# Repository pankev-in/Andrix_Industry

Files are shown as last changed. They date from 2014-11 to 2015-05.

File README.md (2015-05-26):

# Andrix_Industry
AndriX in Industry Use - Practical Robotics Institute Austria (PRIA)

# About this Repository
Here you can find all files, Software and complete documentations used in this Project. Here is a link to a Youtube 
Video, where you can see it in action:
<a href="https://www.youtube.com/watch?v=nksSCDoHSoU">Hedgehog controller drives industrial motor (SCORE! project)</a>

# Who is PRIA?
The Practical Robotics Institute Austria (PRIA) is a non-profit organisation with the aim to promote scien-
tific and technical excellence in schools using robotics as well as the participation and operation of exemplary
research projects in fields related to robotics and automation and teaching methods by means of robotics.
The Practical Robotics Institute Austria is constituted as an independent non-profit organisation with a
scientific advisory board.

# Concept of this Project
Nowadays computers with ARM architecture are becomming more common. Various smartphones, as well
as sigle-board computers like Raspberry Pi are becomming cheaper and much more affordable. To be able
to use ARM Devices as robot controllers, some additional hardware that enables connecting and controlling
robot components such as sensors, motors and servos are required. The hardware (aka. Low-Level Control,
LLC) and the ARM devices(aka. High-Level Control, HLC) should be able to be connected together using
both wired and wireless communications.

Andrix Industry is the concept of implementing this kind of structure in an industrial environment and
its controller has to be relatively low-cost, stable and expandable for different uses.
In this project, we use a standard industrial conveyor belt to test our idea. We will connect our Andrix
controller (including an Raspberry Pi as the High level control) to an external Motor Controller (aka. Ex-
ternal Hardware Controller level) to be able to drive the conveyor belt using a Stepper Motor.

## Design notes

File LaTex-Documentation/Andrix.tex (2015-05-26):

\documentclass[11pt,a4paper]{article}

\usepackage{latexsym}
\usepackage[left=1.5cm,right=1.5cm,bottom=2.5cm,top=2.5cm]{geometry}
\usepackage{tikz} 
\usepackage{mathtools} %Math function
\usepackage{listings} %Source code
\usepackage{pdfpages} %PDF import

\pdfinfo{
	/Title (Andrix-Industry.pdf)
	/Creator (Kevin Pan)
	/Producer (PRIA Austria)
	/Author (Kevin Pan)
	/Subject (Andrix Industry - Sample Usage)
	/Keywords (Andrix, Industry, Sample)
}

\usepackage{graphicx}
\lstset{ 
numbers=left
}

\begin{document}

%----------------------------------------------------------------------------------------
%	TITLE PAGE
%----------------------------------------------------------------------------------------

\begin{titlepage}

\newcommand*{\titlePAGE}{\begingroup % Create the command for including the title page in the document
\hbox{ % Horizontal box
\hspace*{0.1\textwidth} % Whitespace to the left of the title page
\rule{1pt}{\textheight} % Vertical line
\hspace*{0.05\textwidth} % Whitespace between the vertical line and title page text
\parbox[b]{0.75\textwidth}{ % Paragraph box which restricts text to less than the width of the page

{\noindent\Huge\bfseries \textit{Andrix Industry} \\ Sample Usage}\\[2\baselineskip] % Title
{\large \textit{Practical Robotic Institude Austria}}\\
{\large \textit{TGM - The Institute of Technology Austria}}\\[1\baselineskip]
{\large \textbf{2015 May}}\\[4\baselineskip]
{\Large \textsc{Kevin Pan}}\\[1\baselineskip]% Author name
{\Large \textsc{Alexander Wurm}} % Author name

\vspace{0.5\textheight} % Whitespace between the title block and the publisher
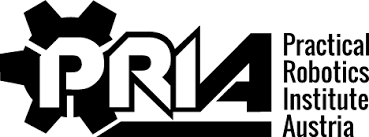
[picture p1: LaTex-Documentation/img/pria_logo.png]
{\noindent  }\\[\baselineskip] % Publisher and logo
}}
\endgroup}

\titlePAGE % This command includes the title page

\end{titlepage}

%----------------------------------------------------------------------------------------
%	CONTENT TABLE
%----------------------------------------------------------------------------------------

\newpage

\tableofcontents

%----------------------------------------------------------------------------------------
%	GENERAL
%----------------------------------------------------------------------------------------

\newpage
\part{Introduction}

	%###################################################
	%	ABOUT
	%###################################################

\section{About}
\subsection{PRIA}
The Practical Robotics Institute Austria (PRIA) is a non-profit organisation with the aim to promote scientific and technical excellence in schools using robotics as well as the participation and operation of exemplary research projects in fields related to robotics and automation and teaching methods by means of robotics. The Practical Robotics Institute Austria is constituted as an independent non-profit organisation with a scientific advisory board.\\

Robots are sophisticated, intelligent systems used in factories and everyday life. They allow students to connect theory with practice and exercise team work, project management, problem solving and communication skills in a stimulating setting. Robotics integrates all the skills needed for designing and constructing machines, computers, software, communications systems and networks. It conveys to students the flexibility needed for developing interdisciplinary projects and discovers exciting topics such as movement, navigation, coordination, physical interaction with objects, audio and video processing, cognition and recognition and many others. It also helps them in developing their abstract thinking and to acquire teamwork skills, independence, imagination and creativity. Experiments with robots include many hands-on experiments that make classes more dynamic and fun.\\

\subsection{Our Mission}

\begin{itemize}
  \item To use robotics technology as an instrument to prepare students to work with various mechanical, electrical and software systems.
  \item To develop environments and tools for teaching robotics that
    \begin{itemize}
    \item will enable simpler programing and control of robots,
    \item are easily interfaced with a broad range of sensors and effectors,
    \item can be used to investigate complex problems and tasks,
    \item are affordable and open for public use.
  \end{itemize}
  \item To introduce appropriate educational methodologies for the successful integration of robotics innovation in school classes.
  \item To organise robotics competitions and measure their educational impact.
  \item Create innovative control architectures for robotics and industrial automation.
  \item Develop knowledge-based systems and agent technology for the automation of flexible industrial processes.
  \item Introduce Augmented Reality and make visualization of industrial processes more efficient and easier to understand.
\end{itemize}

	%###################################################
	%	Concept
	%###################################################
\newpage
\section{Concept}
\subsection{Idea}
Nowadays computers with ARM architecture are becomming more common. Various smartphones, as well as sigle-board computers like Raspberry Pi are becomming cheaper and much more affordable. To be able to use ARM Devices as robot controllers, some additional hardware that enables connecting and controlling robot components such as sensors, motors and servos are required. The hardware (aka. Low-Level Control, LLC) and the ARM devices(aka. High-Level Control, HLC) should be able to be connected together using both wired and wireless communications.\\

\begin{figure}[htp]
	\centering
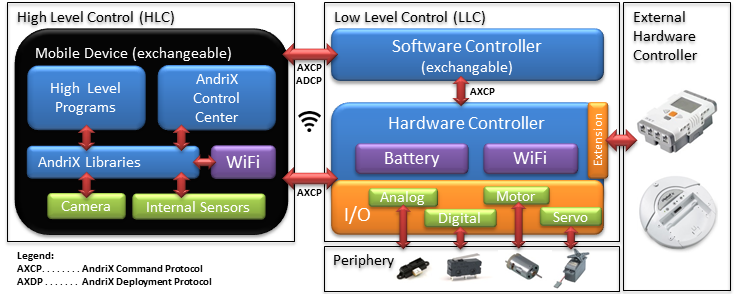
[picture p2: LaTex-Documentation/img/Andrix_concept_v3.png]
	
	\caption{Andrix Concept}
	\label{fig:Andrix Concept v3}
\end{figure}

Andrix Industry is the concept of implementing this kind of structure in an industrial environment and its controller has to be relatively low-cost, stable and expandable for different uses.\\

In this project, we use a standard industrial conveyor belt to test our idea. We will connect  our Andrix controller (including an Raspberry Pi as the High level control) to an external Motor Controller (aka. External Hardware Controller level) to be able to drive the conveyor belt using a Stepper Motor.\\

\begin{figure}[htp]
	\centering
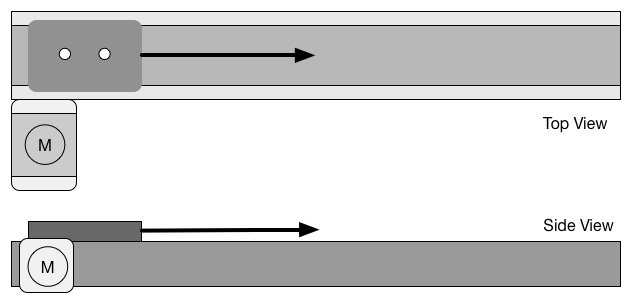
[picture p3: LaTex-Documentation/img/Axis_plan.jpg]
	
	\caption{conveyor belt with NEMA stepper motor}
	\label{fig:Axis Plan}
\end{figure}

THe NEMA Stepper motor series is one of the most popular motors in both amateur and professional fields. They are amazingly  accurate and powerful, but at the same time very easy to control.

	%###################################################
	%	Process
	%###################################################

\newpage
\section{Process}
\subsection{Project steps}
To be able to achive this goal, we planned the project precisely. The following provides a brief overview of our processes:

\begin{enumerate}
\item Choosing matching hardware 
\item Designing necessary mechanical parts
\item Producing mechanical parts by using CNC or 3D-printer 
\item Calculating needed supply power 
\item Designing external motor controller 
\item Prototyping electronic design
\item Communication protocol 
\item Software programming 
\item Debug, test and other final process 
\end{enumerate}

There are some different conditions which have to be satisfied to achieve our concept. At first, we need to find an industrial conveyor belt, which has to be samll enough to let us drive it easily with a stepper-motor without having too many problems. There are mainly two kinds of conveyor belt on the market today - limited and unlimited countineus conveying systems.\\

\subsection{Selecting a suitable conveyor belt}
Unlimited countineus conveying systems are the most common version and have been applied in various areas like raw meterial supply or warehouse transportation systems. They don't need any sesors to detects current position and can be controlled easily by changing the speed of the rotations. Limited conveyor belts work in principle familiar to continues system, but the position of the belt is controlled precisely use servo motor and has integrated sensors working with Hall effect(magnet) or IR encoders(light), but both of them need an extra circuit to drive them and need an externel programme to decode the position.\\

\subsection{Selecting actuator}
This is also one of the reasons why we use a stepper motor. NEMA stepper motors are in comparision to other motors much more flexible. It can be controlled easily with two H-Bridge Motor controller or FET-Transistors. We can dettect the position just by counting the steps in the register from the microcontroller. Of course it also has a disadvantage - speed. The accurency and the speed of the motor are proportional to each other and in our case, this can lead to inaccuracies by changing the step resolution, which is not a mechanical problem that can be easily avoided.\\

\subsection{Communication}
An agreement for the communication protocol between the Andrix and the external motor controller has to be made too. We are using 9600 bit/s as our communication speed. It is a standard bandwidth and can be controlled by other computers. The electronic controller has to be choosed carefully. We have to calculate and test the maximum supply current the motor need to run stably and compare it with the datasheet from the manufactuer.\\

\begin{figure}[htp]
	\centering
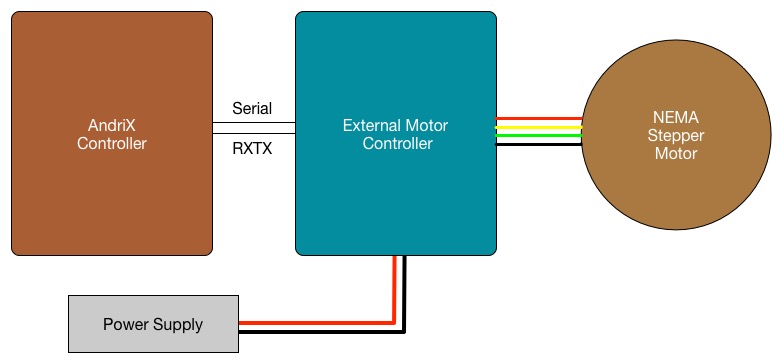
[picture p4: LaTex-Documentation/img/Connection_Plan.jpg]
	
	\caption{Control Flow}
	\label{fig:Axis Plan}
\end{figure}

%----------------------------------------------------------------------------------------
%	DESIGN
%----------------------------------------------------------------------------------------

\newpage
\part{Design}

	%###################################################
	%	Mechanic
	%###################################################
\section{Mechanics}

\subsection{conveyor belt and Axis}

For the conveyor belt, we chose the Bosch RExroth CKR linear motion series. The CKR Compact Modules are precision, ready-to-install linear systems offering high performance within a compact envelope and selectable length, combined with an economical price-to-performance ratio.\\

\textbf{Construction:}
\begin{itemize}
	\item Extremely compact precision aluminum profile with two integrated ball rail guides for optimal movement of heavy loads at high speeds
	\item Ready-to-install Compact Modules in selectable lengths up to Lmax
	\item Short or long aluminum carriage lengths available, depending on application load
	\item Driven by a pre-tensioned, steel-cord reinforced polyurethane toothed belt\\
\end{itemize}

\textbf{Optional Components:}
\begin{itemize}
	\item Maintenance free digital servo drives with integrated brake and pre-installed feedback
	\item Gear Reduced type LP
	\item REED or HALL sensor switches available
	\item Socket with terminals for connection switches
	\item Aluminum profile cable duct for easy mounting of switches\\
\end{itemize}

\textbf{Capabilities:}
\begin{itemize}
	\item Speed - up to 5 m/s
	\item Load Capacity C - up to 56,530 N
	\item Length - up to 5,500mm
	\item Height - 40mm to 65mm
	\item Static Loading - up to 200kg
\end{itemize}

\includepdf[pages=-]{cad/CKR_110_NN_1_69.PDF}
\includepdf[pages=-,landscape]{cad/CKR_110.PDF}

\newpage
\subsection{Actuator and motor}
The motor we are using is QSH5718-76-28-189 from TRINAMIC. It is a two phase hybird stepper motors optimized for microstepping and gives a good fit to high accurate control.\\

\textbf{Specification:}
\begin{itemize}
	\item NEMA 23 mounting Configuration
	\item Number of Leads:	4
	\item Step angle:	1.8
	\item Step Angle Accuracy:	0.05
	\item Holding Torque:	1.89 Nm
	\item Max app. Voltage: 75V
	\item Max Current:	2.8A /Phase	
	\item Max Temp. Rise:	+80
	\item Weight:	1kG
	\item Dimensions(mm):	56.5 x 56.5 x 76
\end{itemize}
\begin{figure}[h!]
	\centering
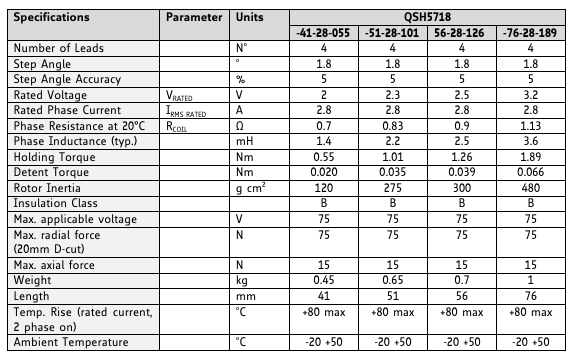
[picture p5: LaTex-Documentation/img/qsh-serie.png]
	
	\caption{Specifications of QSH5718 Series}
	\label{fig:Specifications of QSH5718 Series}
\end{figure}

\includepdf[pages=6-7]{cad/QSH5718_manual.pdf}
\includepdf[pages=10]{cad/QSH5718_manual.pdf}
\includepdf[pages=-,landscape]{cad/Stepper-motor-NEMA-23HS7430.PDF}
\includepdf[pages=-,landscape]{cad/CAD_Assembly.PDF}

	%###################################################
	%	Electronic
	%###################################################
\newpage
\section{Electronics}
\subsection{External motor control unit}

The external motor control unit consists of 2 different boards. One board is responsible for communication and translates the commands from the Andriox controler to the actual PWM signal and direction output. Another part of this unit is the motor controller. As the requirement, our stepper motor is bipolar and contents 4 wires. Two in a pair and each pair is only responsible for one coil.\\

\begin{figure}[h!]
	\centering
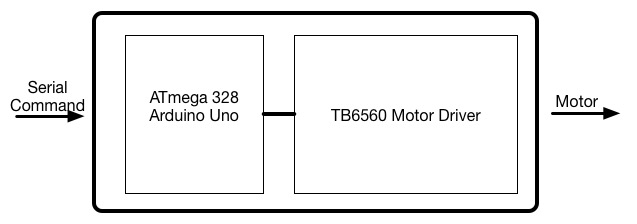
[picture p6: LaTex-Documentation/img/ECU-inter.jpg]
	
	\caption{ECU Overview}
	\label{fig:ECU Overview}
\end{figure}

For communication we decided to use a prototype board - Arduino uno. On the board is a ATmega 328 and has built-in serial communication pins. The standard Arduino IDE has pre implemented libraries for both serial and PWM signals.\\

The same as the describtion from the NEMA 23 Motor data sheet, we also found a stepper motor driver with required output current. The core of this board is a Toshiba dual H-bridge chip TB6560.\\

%Motor Requierment and Data sheet from tb6560 motor driver
\begin{table}[h!]
\centering
\begin{tabular}{ ||l | l ||}
	\hline
	Model & QSH 5718-76-28-189\\
	Max. Voltage & 75 V\\
	Rated phase current & 2.8 A\\
	Number of leads & 4\\
	\hline
\end{tabular}
\caption{NEMA 23 requierment} 
\end{table}
\begin{table}[h!]
\centering
\begin{tabular}{|| l | l ||}
	\hline
	Operating Voltage & 12 - 36 V\\
	Max. Output current & 1.5 - 3 A/phase\\
	Drive type & Double-pole const. PWM\\
	Compatible Stepper motors & 4/6/8 leads\\
	\hline
\end{tabular}
\caption{TB6560 Data sheet} 
\end{table}

\begin{figure}[h!]
	\centering
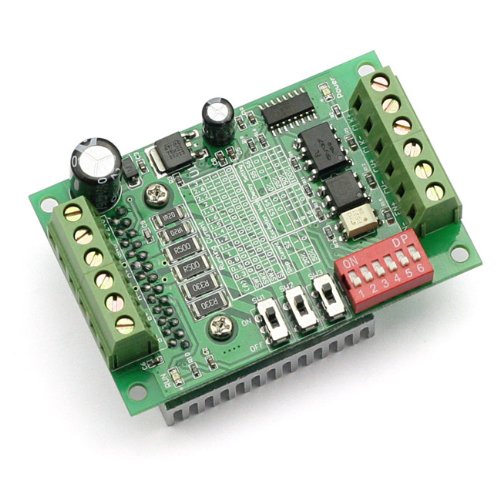
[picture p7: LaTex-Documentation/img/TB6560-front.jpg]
	
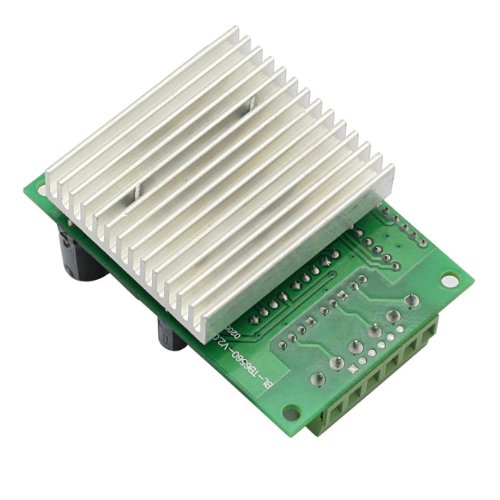
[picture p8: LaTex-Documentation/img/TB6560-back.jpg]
	
	\caption{TB6560 Stepper Motor Driver Module}
	\label{fig:TB6560 Stepper Motor Driver Module}
\end{figure}

\subsection{Power supply}

As we are suppplying our motor with 12V, the calculation of the power consumption will be like this:\\

\begin{equation}
   \text{Total power }P_t  = \text{External Control Unit } P_e + \text{Motor }P_m
\end{equation}
\begin{equation}
   P_m = I_o \times U_i = 3A \times 12V = 36 W 
\end{equation}
\begin{equation}
   P_m \gg P_e \text{ ,so }  P_m \approx P_t
\end{equation}
\\

Our power supply must able to supply at least 40 Watts of power to drive our converying belt and control units.

\newpage
\subsection{Overall circuit}

\begin{figure}[h!]
	\centering
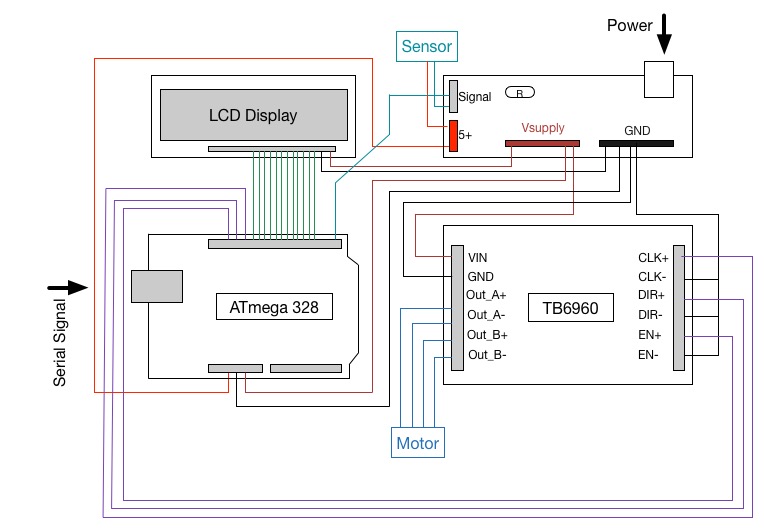
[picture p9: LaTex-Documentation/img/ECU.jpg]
	
	\caption{External Control Unit: cabling}
	\label{fig:External Control Unit: cabling}
\end{figure}

	%###################################################
	%	Software
	%###################################################
\newpage
\section{Software - Ecu}
\subsection{Logical equivalence }
The system logic of the external motor controller has 3 main states: initial, processing and waiting process:\\
\begin{figure}[h!]
	\centering
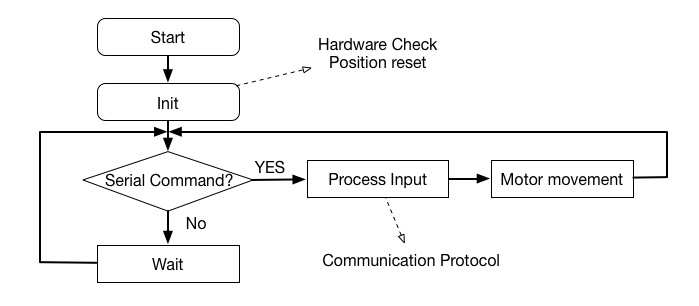
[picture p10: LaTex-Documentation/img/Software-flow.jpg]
	
	\caption{Software Logic}
	\label{fig:Software logic}
\end{figure}\\

In the boot up phase, the system will first check if all the hardware is connected and reset the position automatically. It sends continuous signals to the motor to move the conveying base back to the origin and if the base has a physical contact with it, the digital sensor will set its output to HIGH.\\

After the reboot, the system is ready and waits for the serial command from the andrix or PCs. The serial bandwidth has already been set in the initial process and the default is 9600bit/s. Any serial signal during the waiting phase will be stored in a String buffer to futher process. The conmunication will be base on the protocol from \textbf{section 6.3}.

\subsection{Function description}
To find more detail of a specific function, please go to \textbf{section 6.4}.\\
\begin{table}[h!]
\centering
\begin{tabular}{ |l | l | c |c |}
	\hline
	Name & Use & Input & Return\\
	\hline
	setup() & Init Setup & --- & ---\\
	loop() & Main loop & --- & depend\\
	serialEvent() & Reading Serial Input and buffer them & --- & ---\\
	reset() & Reset position to origin & --- & ---\\
	goToPosition() & Go to position & Integer & ---\\
	lcdShow() & Display message on LCD Display & String 1,2 & ---\\
	lcdBackLightOnOff()   & Turn LCD Light On or Off & boolean & ---\\
	\hline
	
\end{tabular}
\end{table}

\newpage
\subsection{Communication protocol}
\begin{table}[h!]
\centering
\begin{tabular}{ ||l | l | l ||}
	\hline
	Command & Description & Sample\\
	...@ & @ - end; ... - Commands & Bandwith = 9600 bit/sec \\ \hline\hline
	ENA@ &Enable the motor & Send: \textbf{ENA@} -- Motor enabled\\
	DIS@ &Disable the motor& Send: \textbf{DIS@} -- Motor disabled\\
	RES@ &Reset, back to origin& Send: \textbf{RES@} -- Axis back to 0 position\\
	GTP...@ & Go to xxx/10 mm position	[Max. 4950]& Send: \textbf{GTP1234@} -- Axis go to 123.4mm\\
	SST...@ & Set delay of motor(default 0)	[2 byte]& Send: \textbf{SST1@} -- Set 1 ms delay for each step\\
	CTP@ & send back to the current position [2 byte]& Send: \textbf{CTP@};Return: \textbf{123@}  -- Current Position\\
	CTS@ & send back the current speed(delay) [2 byte]& Send: \textbf{CTS@};Return: \textbf{1@}  -- Current Delay\\	
	LED...@ & Turn LED Display light ON or Off & Send: \textbf{LED1@}--Light turn On\\
		\hline
\end{tabular}
\caption{Protocol: Stepper Motor Control} 
\end{table}

If you want to modify the setting of the communication bandwidth, you will have to programme the external control unit with the source code from \textbf{6.4} using Arduino IDE.\\

\textbf{Communication sample:}
\begin{lstlisting}
Normal Operation:
1.SEND:		ENA@		\\Enables the motor
2.SEND:		GTP1000@	\\Go to Position 10cm
3.SEND:		RES@		\\Reset position to 0, all default value

Move Slowly:
1.SEND:		ENA@		\\Enables the motor
2.SEND:		SST1@		\\Set Delay for 1ms
3.SEND:		GTP500@		\\Convayingbelt will move slowly to 5cm

Let conveyor belt to be able to move by hand:
1.SEND:		DIS@		\\Disable the motor
2.SEND:		RES@		\\WARNING:You must reset the position!

Turn On/Off LED Display backlight:
1.SEND:		LED1@		\\Turn On light
2.SEND:		LED0@		\\Turn Off light
3.SEND:		LED3@		\\Turn On light(Any num.>0 will be 'ON')

\end{lstlisting}

\newpage
\subsection{Source code}
\lstinputlisting[language=C]{code/Stepper_Low_Power.c}

%----------------------------------------------------------------------------------------
%	CONCLUTION
%----------------------------------------------------------------------------------------
\newpage
\part{Conclution} 
After assembling the mechanical design and putting all electronic components together, we devised a very simple system. We tested the axis accuracy and it is much more percise than we first expected.\\
\section{Resaults and Comparison}

In comparison with some of the industrial standard machines, our solution can be up to 10 times cheaper. Of course, the standard system can control/supply multiple linear or even other kinds of axises at the same time. But one of the biggest advantages of distributed system is flexibility.\\

Unter the same kind of hardware structure, we are able to connect multiple controllers with a central computer, and control them induvidually. It is also even posible to implement some kind of smart algorithm, which is designed spicificly for each individual enviroment.\\

In this example we only show one way of using an Andrix controller in Industrial area. It shows us the potential of distributed system and can be one of the most important keys for 'Industrial 4.0'. It will change the way we look at the normal rigid structure.\\

\end{document}
\grid
\grid

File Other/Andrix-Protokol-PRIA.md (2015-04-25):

## Andrix - Protokol: PRIA

### About PRIA(Wurm)[1]

### Team(Wurm)[1]

### Concepte(PAN)[2]
* Was ist Andrix?
* Vorteile?
* Unsere Idee mit Andrix Industrie?
* Concept plan

### Umsetzung(PAN)[1]
* Arbeitsschritte
* Unterschiede zwischen 2 motoren/Achsen
* Wir nehmen NEMA 23 als Beispiel

### Mechanic(PAN)[3,4]
* Achse:
	* Model nummer
	* länge/breite/gröse
	* beschränkungen zu beachten
	* Datenblatt (falls es gibt)
	* CAD Zeichnung 
* Motor:
	* Gröse, Stärke 
	* Drehmoment
	* Maximale Drehzahl
	* Datenblatt
	* CAD Zeichung
* Wellenadapter:
	* Warum brauchen wir es? Problem beschreibung
	* Meterial Auswall
	* Messungen
	* CAD Zeichnung
* Gesamt:
	* Messungen
	* CAD Zeichnung  
* Fotos von end produkten

### Electronik(Wurm)[3]
* Andrix:
* External Motor Steuerung:
	* Welche leistung hat der motor? 
	* Welche leistung muss diese Krontroller treiben können?
	* Steuerungsverlauf
		* Bild
		* Beschreibung
	* Power supply
	* Interne Schaltungs plan (friztzing oder co.)
* Fotos von end produkten

### Software(Wurm)[3,4]
* Control bzw. Logische Verlauf
* Funktion beschreibung
* Source Code mit genaue Commendar dazu

### Conclutions(PAN)[2]
* Testergebnisse: Gut? Schlecht?
* Vergleich mit Industrie Standard Steuerung:
	* Preis
	* Flexibilität
	* Erweiterungsmöglichkeit(Open Source?)
	* Größe
* Idee mit Industrie 3.0 zusammen verbinden

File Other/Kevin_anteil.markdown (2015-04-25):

## Concept

Nowadays computers under ARM architecture are getting common. Variate smartphones, sigle-board computers like Raspberry Pi are getting cheaper and much more affordable. To be able to use ARM Devices as robot controllers, some additional hardware that enables connecting and controlling robot components such as sensors, motors and servos are required. The hardware (aka. Low-Level Control, LLC) and the ARM devices(aka. High-Level Control, HLC) should be able to be connected together using both wired and wireless communications. The following figure illustrates the concept:



AndriX Industry is the concept of implementing this kind of structure in a industrial environment and its controller has to be low-cost(relatively), stable and expansional for different uses.

In this project, we are using a standard industrial conveying belt to test our idea. We will connect  our Andrix controller (including an Raspberry Pi as the High level control) to a external Motor Controller (aka. External Hardware Controller level) to be able to drive the conveying belt using a Stepper Motor.

NEMA Stepper motor series is one of the most popular Motors in both pre-industrial and professional fields. It is amazingly  accurate and powerful, but at the same time very easy to control.

## Processes

To be able to achive the goal, we planned the project precisely and here is a quick overall view of our working processes:

1. Choosing matching hardware
2. Designing other mechanical parts we need
3. Producing mechanic parts by using CNC or 3D-printer
4. Calculate needed supply power 
5. Design external motor controller
6. Prototyping electronic design
7. Communication protocol
8. Software programming
9. Debug, test and other finalisation process

There are some different conditions have to be satisfied to achieve our concept. At first, we need to find a industrial conveying belt, which has to be samll enough to let us drive it easily with one stepper-motor without having too many problems. There are mainly two kind of conveying belt on the market today - limited and unlimited countineus conveying Systems. 

Unlimited countineus conveying systems are the most common version and have been applicated in various areas like raw meterial supplyment or warehaus transportation systems. They don’t need any sesors to detect current position and can be controlled easily by changing the speed of the rotations. Limited conveying belts works in principle familiar to countineus system, but the position of the belt is controlled precisely using servo motor and has integrated sensors working with hall effect(magnet) or IR encoders(light), but both of them need extra circuit to drive them and need externel programm to decode the position.

This is also one of the reason why we use stepper motor. NEMA stepper motors are in compare to other motors much more flexible to control. It can be controlled pretty easily with two H-Bridge Motor controller or FET-Transistors. We can dettect the position just by counting the steps in the register from the microcontroller. Of course it also has disadvantage - speed. The accurency and the speed of the motor are proportional to each other and in our case, we can lose our accurency by changing the step resolution, which isn’t a mechanical problem that can be simply avoided.

An agreement for the communication protocol between the andrix and the external motor controller has to be made too. We are using 9600 bit/s as our communication speed. It is a standard bandwitdh and can be even controlled with other computers. The electronic controllers has to be choosed carefully. We have to calculate and test the maximum supply current the motor needed to run stabely and compare it with the datasheet from the manufacture.

## Mechanic
### Overview:IEF profiLine 140
### Conveying belt
### Motor
### Shaft Adapter

## Conclutions

aasdfas

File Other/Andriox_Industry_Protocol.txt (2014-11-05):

Androix Industry: Industrie Motor / Robotic Steuerung
  Autor: Kevin Pan
  Date: 09.2014 - 11.2014

###############################################################################
Introduction:

  "Androix" Controller is an easy-to-programm, educational robotic controller.It
  is developed by Practical Robotic Institute Austria (As known as PRIA). Located
  at TGM, a technical Institute in Vienna, Austria.

  Andriox is designed for everybody, who wanted to build their own DIY-Robots,
  but didn't know where to start with. Andriox allows users to program their
  robot without any knowledges. You can simply program the robot using any kind
  of smartphones. There are graphical API for Androix running on Android, IOS,
  Windows, OSX or even Linux.

  The basic Idea of the "Androix-Industry" project is to use this simple controller
  to controll Industrial-level Motors/Axis. Which allows the Instructors to have
  a low-cost, stable, expansional to achieve the Idea of "Industrial 3.0".

###############################################################################
Setup:

  In this project, we are using NEMA Stepper motors to test our idea. NEMA
  Stepper-motor series is one of the most popular Motors for both pre-industrial
  uses and professional levels. It is very accurate and powerful, but at the same
  time easy to control.

  We chose two kind of NEMA Motors here:
    - 1x NEMA 23 (QSH 5718-76-28-189)
    - 1X NEMA 34 (QSH 8618-96-55-700)

  Both motor above are standard motors, which has been used in Robotic Industry
  or even as light-weight machine axis. NEMA 23/34 operates normally between
  12-24 V and requiers a extern power supply. But to be able to control the motor,
  we would need a extension module between the Androix Controller and the actual
  physical Motor.

  Here is the Controll flow(foto):

                  ########################################
                  #                                      #
                  #                                      #
                  #                                      #
                  #                                      #
                  #                                      #
                  ########################################

###############################################################################
Extension-Module:

  NEMA 23 specification:
      ∙ Type: Bipolar Stepper motor (4 wires)
      ∙ Ideal Voltage: 12-24 V (Vmax: 75V)
      ∙ Stall current: 2.8A (Max)

  NEMA 34 specification:
      ∙ Type: Bipolar Stepper motor (4 wires)
      ∙ Ideal Voltage: 24-36 V (Vmax: 75V)
      ∙ Stall current: 5.5A (Max)

  Control Module requirements:
      ∙ Stable
      ∙ Accuration
      ∙ Read serial commands from Androix
      ∙ Minimal Connections between the Controller and Androix
      ∙ Supply Motor with ideal voltage/current
      ∙ Scalability

###############################################################################
Andoix-Programming:

###############################################################################
Stability:

###############################################################################
Cost:

###############################################################################
Expansibility:

###############################################################################
Summary:

###############################################################################
Contact:

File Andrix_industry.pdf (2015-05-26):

# Andrix Industry Sample Usage

Practical Robotic Institude Austria
TGM - The Institute of Technology Austria

2015 May

Kevin Pan

Alexander Wurm

## Contents

I | Introduction | 2
1 About | 2
2 Concept | 3
3 Process | 4
II | Design | 6
4 Mechanics | 6
5 Electronics | 16
6 Software - Ecu | 19
III | Conclution | 26
7 Resaults and Comparison | 26

## Part I

# Introduction

## 1 About

### 1.1 PRIA

The Practical Robotics Institute Austria (PRIA) is a non-profit organisation with the aim to promote scientific and technical excellence in schools using robotics as well as the participation and operation of exemplary research projects in fields related to robotics and automation and teaching methods by means of robotics. The Practical Robotics Institute Austria is constituted as an independent non-profit organisation with a scientific advisory board.

Robots are sophisticated, intelligent systems used in factories and everyday life. They allow students to connect theory with practice and exercise team work, project management, problem solving and communication skills in a stimulating setting. Robotics integrates all the skills needed for designing and constructing machines, computers, software, communications systems and networks. It conveys to students the flexibility needed for developing interdisciplinary projects and discovers exciting topics such as movement, navigation, coordination, physical interaction with objects, audio and video processing, cognition and recognition and many others. It also helps them in developing their abstract thinking and to acquire teamwork skills, in-dependence, imagination and creativity. Experiments with robots include many hands-on experiments that make classes more dynamic and fun.

### 1.2 Our Mission

- To use robotics technology as an instrument to prepare students to work with various mechanical, electrical and software systems.
- To develop environments and tools for teaching robotics that

– will enable simpler programing and control of robots,

– are easily interfaced with a broad range of sensors and effectors,

– can be used to investigate complex problems and tasks,

– are affordable and open for public use.

- To introduce appropriate educational methodologies for the successful integration of robotics innova-tion in school classes.
- To organise robotics competitions and measure their educational impact.
- Create innovative control architectures for robotics and industrial automation.
- Develop knowledge-based systems and agent technology for the automation of flexible industrial processes.
- Introduce Augmented Reality and make visualization of industrial processes more efficient and easier to understand.

## 2 Concept

### 2.1 Idea

Nowadays computers with ARM architecture are becomming more common. Various smartphones, as well as sigle-board computers like Raspberry Pi are becomming cheaper and much more affordable. To be able to use ARM Devices as robot controllers, some additional hardware that enables connecting and controlling robot components such as sensors, motors and servos are required. The hardware (aka. Low-Level Control, LLC) and the ARM devices(aka. High-Level Control, HLC) should be able to be connected together using both wired and wireless communications.

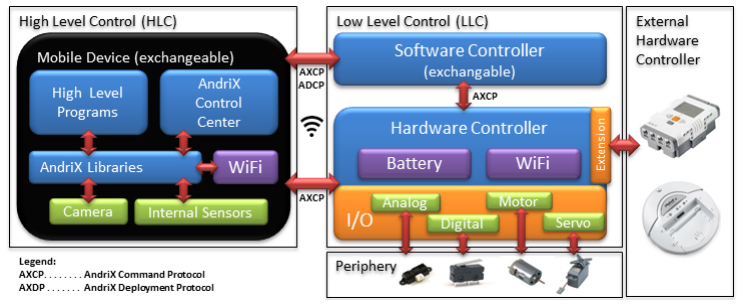
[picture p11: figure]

Figure 1: Andrix Concept

Andrix Industry is the concept of implementing this kind of structure in an industrial environment and its controller has to be relatively low-cost, stable and expandable for different uses.

In this project, we use a standard industrial conveyor belt to test our idea. We will connect our Andrix controller (including an Raspberry Pi as the High level control) to an external Motor Controller (aka. External Hardware Controller level) to be able to drive the conveyor belt using a Stepper Motor.


Figure 2: conveyor belt with NEMA stepper motor

THe NEMA Stepper motor series is one of the most popular motors in both amateur and professional fields. They are amazingly accurate and powerful, but at the same time very easy to control.

## 3 Process

### 3.1 Project steps

To be able to achive this goal, we planned the project precisely. The following provides a brief overview of our processes:

1. Choosing matching hardware
2. Designing necessary mechanical parts
3. Producing mechanical parts by using CNC or 3D-printer
4. Calculating needed supply power
5. Designing external motor controller
6. Prototyping electronic design
7. Communication protocol
8. Software programming
9. Debug, test and other final process

There are some different conditions which have to be satisfied to achieve our concept. At first, we need to find an industrial conveyor belt, which has to be samll enough to let us drive it easily with a stepper-motor without having too many problems. There are mainly two kinds of conveyor belt on the market today -limited and unlimited countineus conveying systems.

### 3.2 Selecting a suitable conveyor belt

Unlimited countineus conveying systems are the most common version and have been applied in various areas like raw meterial supply or warehouse transportation systems. They don’t need any sesors to detects current position and can be controlled easily by changing the speed of the rotations. Limited conveyor belts work in principle familiar to continues system, but the position of the belt is controlled precisely use servo motor and has integrated sensors working with Hall effect(magnet) or IR encoders(light), but both of them need an extra circuit to drive them and need an externel programme to decode the position.

### 3.3 Selecting actuator

This is also one of the reasons why we use a stepper motor. NEMA stepper motors are in comparision to other motors much more flexible. It can be controlled easily with two H-Bridge Motor controller or FET-Transistors. We can dettect the position just by counting the steps in the register from the microcontroller. Of course it also has a disadvantage - speed. The accurency and the speed of the motor are proportional to each other and in our case, this can lead to inaccuracies by changing the step resolution, which is not a mechanical problem that can be easily avoided.

### 3.4 Communication

An agreement for the communication protocol between the Andrix and the external motor controller has to be made too. We are using 9600 bit/s as our communication speed. It is a standard bandwidth and can be controlled by other computers. The electronic controller has to be choosed carefully. We have to calculate and test the maximum supply current the motor need to run stably and compare it with the datasheet from the manufactuer.


Figure 3: Control Flow

## Part II

# Design

## 4 Mechanics

### 4.1 conveyor belt and Axis

For the conveyor belt, we chose the Bosch RExroth CKR linear motion series. The CKR Compact Modules are precision, ready-to-install linear systems offering high performance within a compact envelope and selectable length, combined with an economical price-to-performance ratio.

Construction:

- Extremely compact precision aluminum profile with two integrated ball rail guides for optimal movement of heavy loads at high speeds
- Ready-to-install Compact Modules in selectable lengths up to Lmax
- Short or long aluminum carriage lengths available, depending on application load
- Driven by a pre-tensioned, steel-cord reinforced polyurethane toothed belt

Optional Components:

- Maintenance free digital servo drives with integrated brake and pre-installed feedback
- Gear Reduced type LP
- REED or HALL sensor switches available
- Socket with terminals for connection switches
- Aluminum profile cable duct for easy mounting of switches

Capabilities:

- Speed - up to 5 m/s
- Load Capacity C - up to 56,530 N
- Length - up to 5,500mm
- Height - 40mm to 65mm
- Static Loading - up to 200kg

# CKR 15-110 dimensions

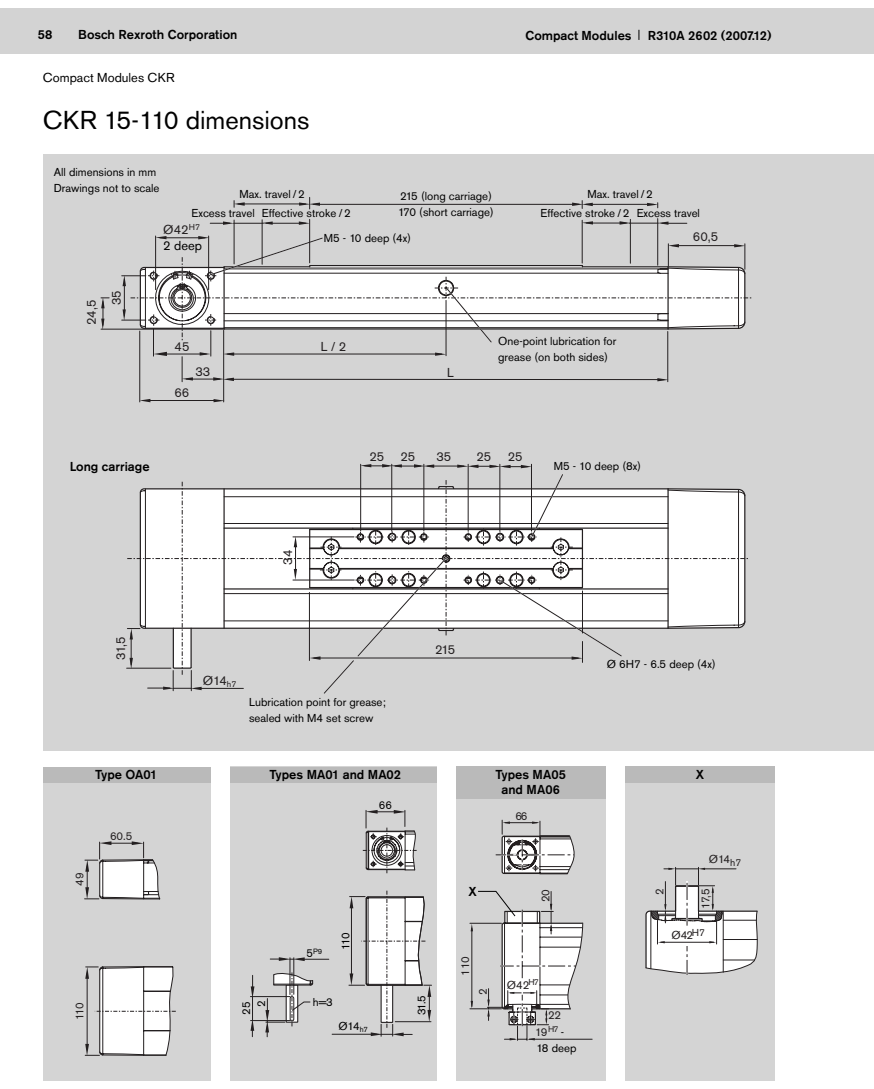
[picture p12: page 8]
Bosch Rexroth Corporation; Compact Modules; Long carriage; M5 - 10 deep (8x); 215 (long carriage) 170 (short carriage); M5 - 10 deep (4x); Max. travel/2; Ø 6H7 - 6.5 deep (4x); - 18 deep; Type OA01; Types MA01 and MA02; Types MA05; and MA06

Compact Modules CKR

All dimensions in mm
Drawings not to scale

Excess travel Effective stroke /2
2 deep

Effective stroke /2 Excess travel

One-point lubrication for
grease (on both sides)

Lubrication point for grease;
sealed with M4 set screw

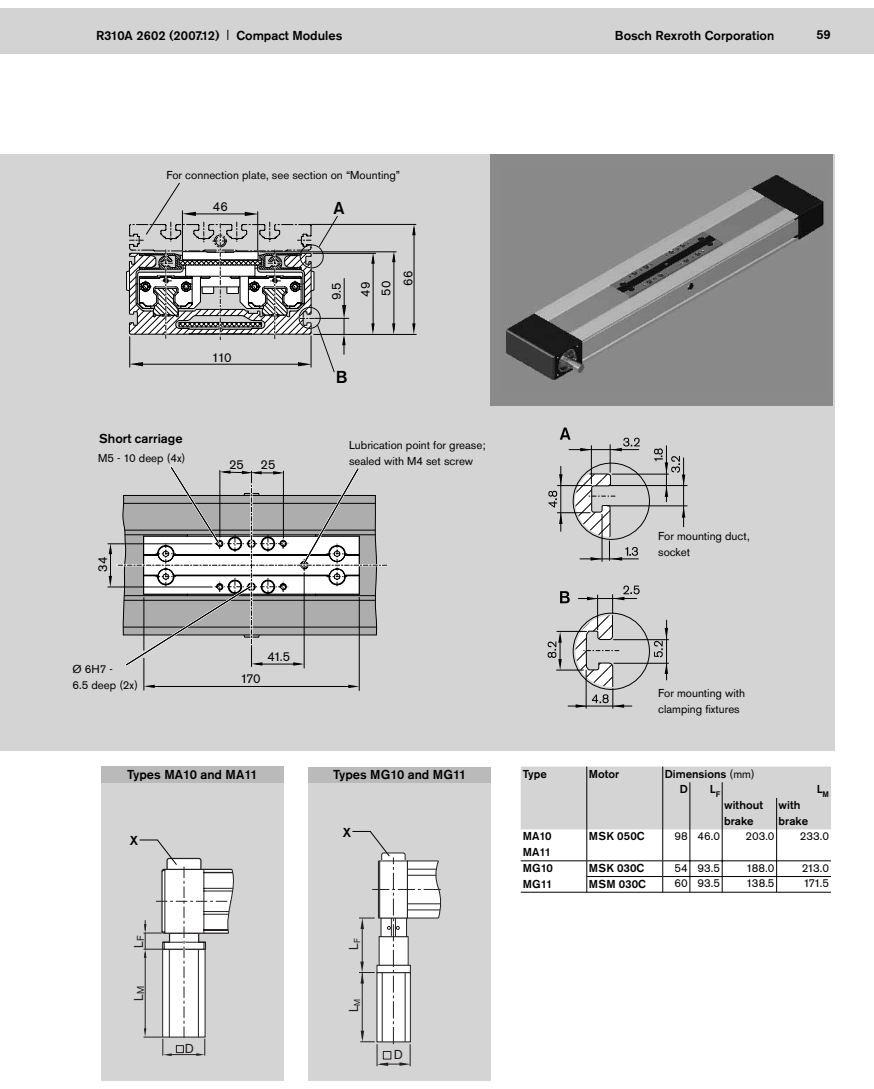
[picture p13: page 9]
Compact Modules; Bosch Rexroth Corporation; Short carriage; M5 - 10 deep (4x); Ø 6H7 - 6.5 deep (2x); MSK 050C; MSK 030C; MSM 030C; Types MA10 and MA11; Types MG10 and MG11

For connection plate, see section on “Mounting”

Lubrication point for grease;
sealed with M4 set screw

For mounting duct,
socket

For mounting with
clamping fi xtures

Type | Motor | Dimensions (mm)

without brake | with brake

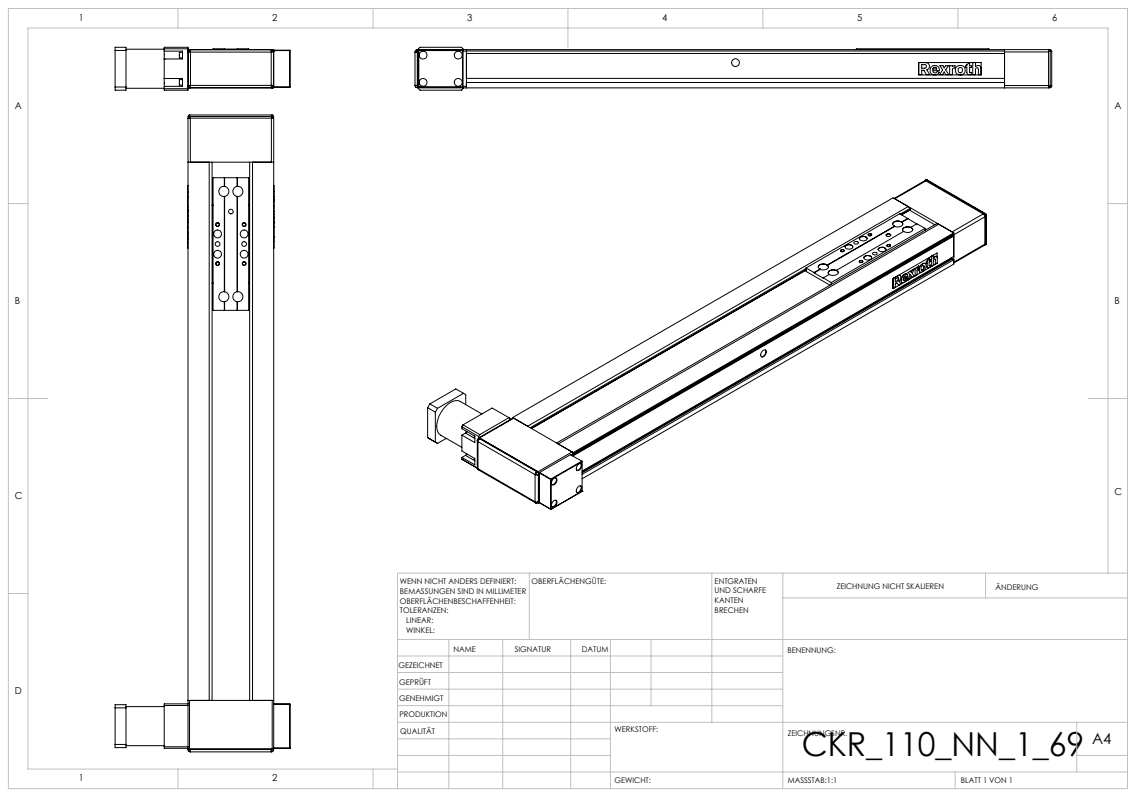
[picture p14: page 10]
OBERFLÄCHENGÜTE:; ENTGRATEN; UND SCHARFE KANTEN BRECHEN; ZEICHNUNG NICHT SKALIEREN; ÄNDERUNG; MASSSTAB:1:1; BLATT 1 VON 1; GEWICHT:

WENN NICHT ANDERS DEFINIERT:
BEMASSUNGEN SIND IN MILLIMETER
OBERFLÄCHENBESCHAFFENHEIT:
TOLERANZEN:
LINEAR:
WINKEL:

NAME | SIGNATUR | DATUM | | | | BENENNUNG:

GEZEICHNET
GEPRÜFT
GENEHMIGT
PRODUKTION
QUALITÄT | | | | WERKSTOFF: | CKR_110_NN_1_69 ZEICHNUNGSNR. | A4

### 4.2 Actuator and motor

The motor we are using is QSH5718-76-28-189 from TRINAMIC. It is a two phase hybird stepper motors optimized for microstepping and gives a good fit to high accurate control.

Specification:

- NEMA 23 mounting Configuration
- Number of Leads: 4
- Step angle: 1.8
- Step Angle Accuracy: 0.05
- Holding Torque: 1.89 Nm
- Max app. Voltage: 75V
- Max Current: 2.8A /Phase
- Max Temp. Rise: +80
- Weight: 1kG
- Dimensions(mm): 56.5 x 56.5 x 76

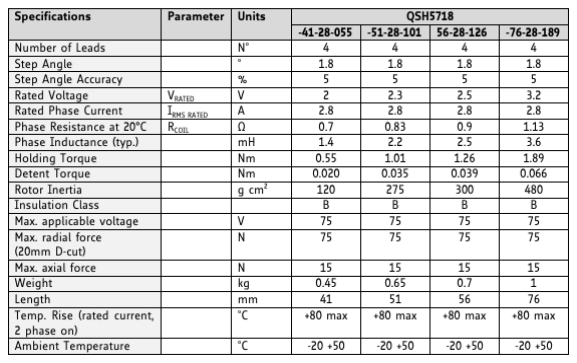
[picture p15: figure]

Figure 4: Specifications of QSH5718 Series

# 4 Mechanical dimensions

## 4.1 Dimensions

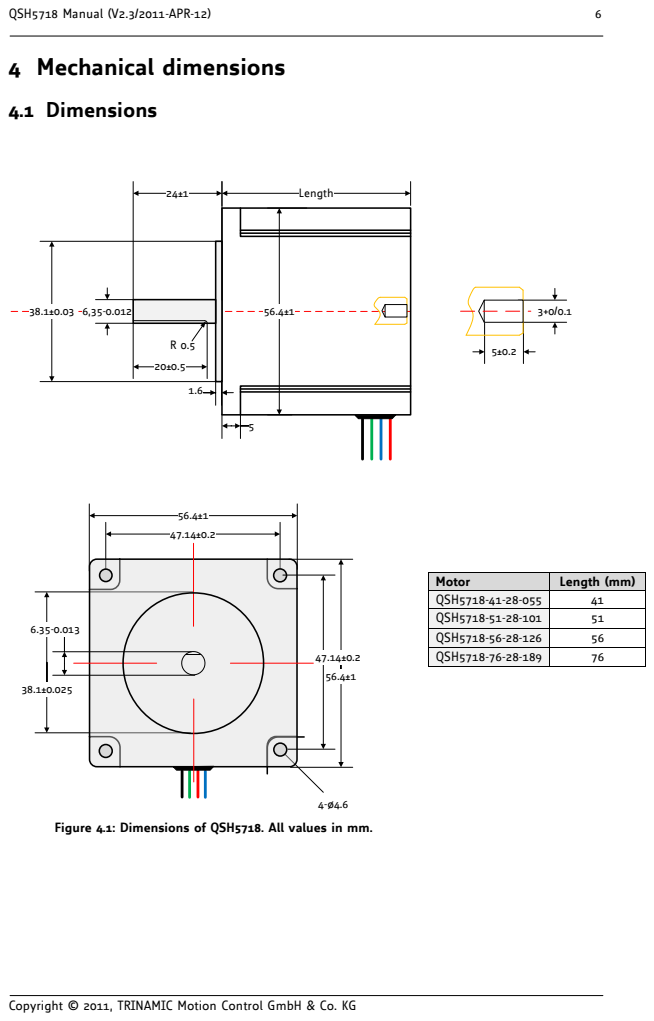
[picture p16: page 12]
QSH5718 Manual (V2.3/2011-APR-12); Length

Motor | Length (mm)
QSH5718-41-28-055 | 41
QSH5718-51-28-101 | 51
QSH5718-56-28-126 | 56
QSH5718-76-28-189 | 76

Figure 4.1: Dimensions of QSH5718. All values in mm.

Copyright © 2011, TRINAMIC Motion Control GmbH & Co. KG

QSH5718 Manual (V2.3/2011-APR-12) | 7

Copyright © 2011, TRINAMIC Motion Control GmbH & Co. KG

## 4.2 Leadwire configuration

M black

green

red

blue

A B

Figure 4.2: Leadwire configuration

Cable type 1 | Gauge | Coil | Function
Black | UL1007 AWG22 | A | Motor coil A pin 1
Green | UL1007 AWG22 | A- | Motor coil A pin 2
Red | UL1007 AWG22 | B | Motor coil B pin 1
Blue | UL1007 AWG22 | B- | Motor coil B pin 2

QSH5718 Manual (V2.3/2011-APR-12) | 10

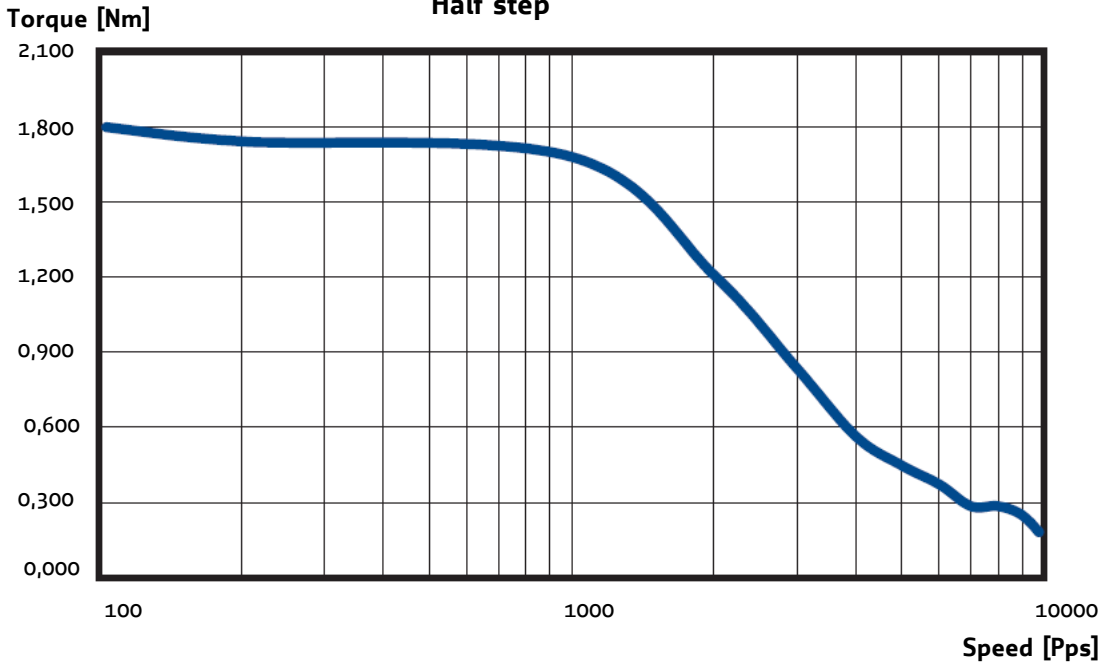
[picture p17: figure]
10000 Speed [Pps]; Torque [Nm] 2,100

Copyright © 2011, TRINAMIC Motion Control GmbH & Co. KG

## 5.4 QSH5718-76-28-189

VM: 30V, 2,8A/Phase

### Half step

Figure 5.4: QSH5718-76-28-189 speed vs. torque characteristics

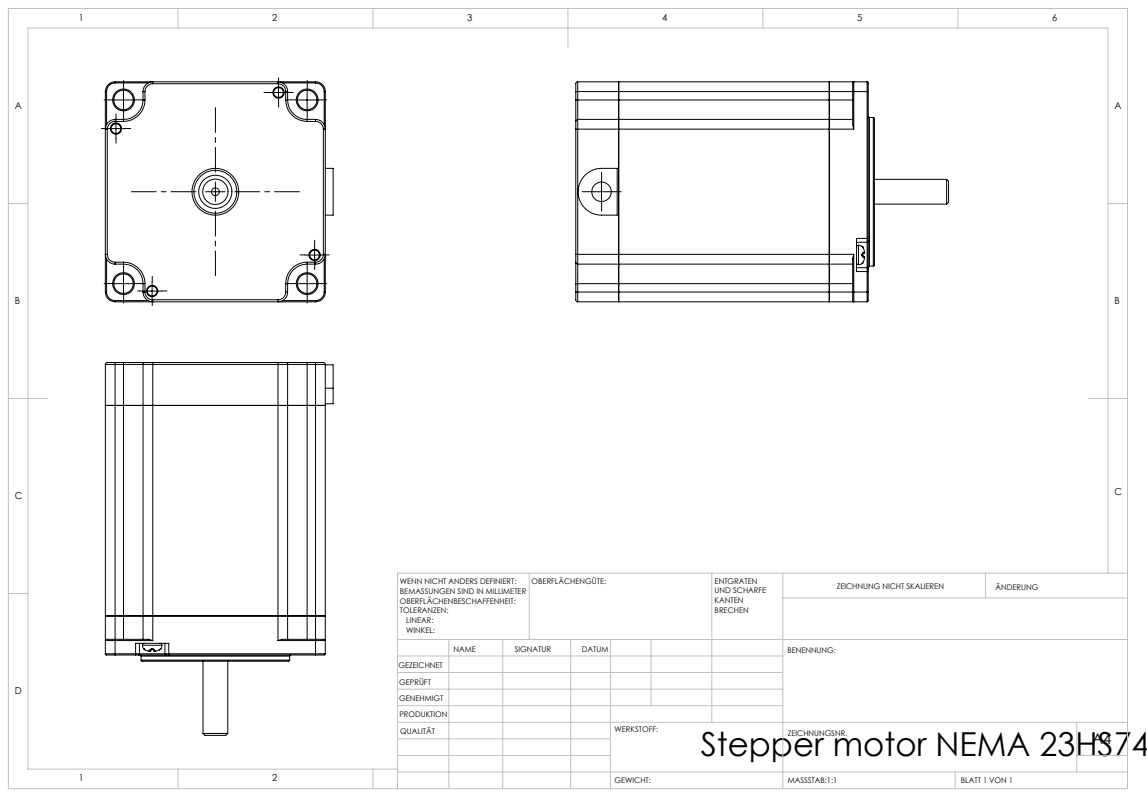
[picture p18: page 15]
OBERFLÄCHENGÜTE:; ENTGRATEN; UND SCHARFE KANTEN BRECHEN; ZEICHNUNG NICHT SKALIEREN; ÄNDERUNG; MASSSTAB:1:1; BLATT 1 VON 1; GEWICHT:

WENN NICHT ANDERS DEFINIERT:
BEMASSUNGEN SIND IN MILLIMETER
OBERFLÄCHENBESCHAFFENHEIT:
TOLERANZEN:
LINEAR:
WINKEL:

NAME | SIGNATUR | DATUM | | | | BENENNUNG:

GEZEICHNET
GEPRÜFT
GENEHMIGT
PRODUKTION
QUALITÄT | | | | WERKSTOFF: | ZEICHNUNGSNR. | A4

Stepper motor NEMA 23HS7430

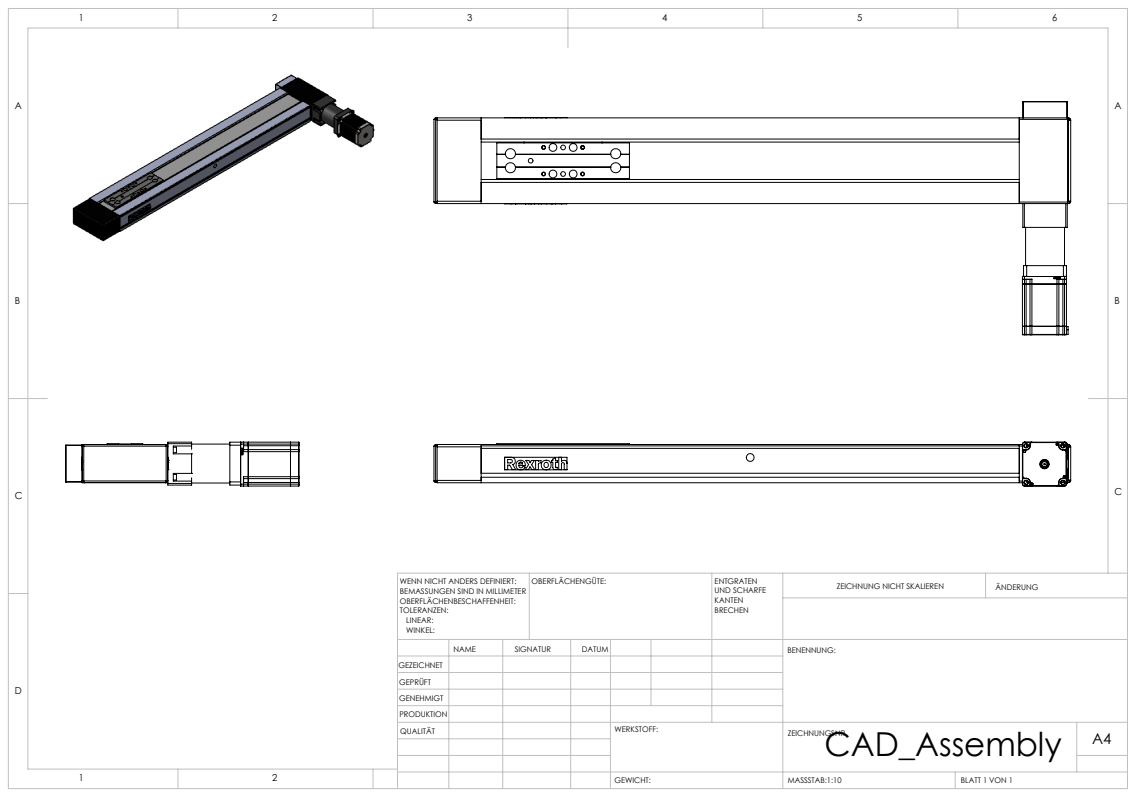
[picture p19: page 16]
OBERFLÄCHENGÜTE:; ENTGRATEN; UND SCHARFE KANTEN BRECHEN; ZEICHNUNG NICHT SKALIEREN; ÄNDERUNG; MASSSTAB:1:10; BLATT 1 VON 1; GEWICHT:

WENN NICHT ANDERS DEFINIERT:
BEMASSUNGEN SIND IN MILLIMETER
OBERFLÄCHENBESCHAFFENHEIT:
TOLERANZEN:
LINEAR:
WINKEL:

NAME | SIGNATUR | DATUM | | | | BENENNUNG:

GEZEICHNET
GEPRÜFT
GENEHMIGT
PRODUKTION
QUALITÄT | | | | WERKSTOFF: | CAD_Assembly ZEICHNUNGSNR. | A4

## 5 Electronics

### 5.1 External motor control unit

The external motor control unit consists of 2 different boards. One board is responsible for communication and translates the commands from the Andriox controler to the actual PWM signal and direction output. Another part of this unit is the motor controller. As the requirement, our stepper motor is bipolar and contents 4 wires. Two in a pair and each pair is only responsible for one coil.

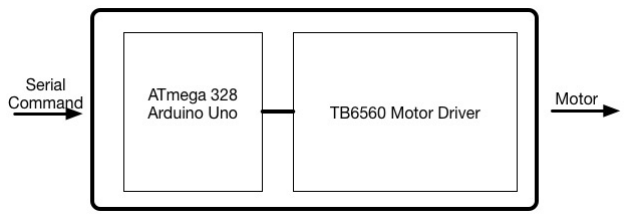
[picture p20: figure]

Figure 5: ECU Overview

For communication we decided to use a prototype board - Arduino uno. On the board is a ATmega 328 and has built-in serial communication pins. The standard Arduino IDE has pre implemented libraries for both serial and PWM signals.

The same as the describtion from the NEMA 23 Motor data sheet, we also found a stepper motor driver with required output current. The core of this board is a Toshiba dual H-bridge chip TB6560.

Model | QSH 5718-76-28-189
Max. Voltage | 75 V
Rated phase current | 2.8 A
Number of leads | 4

Table 1: NEMA 23 requierment

Operating Voltage | 12 - 36 V
Max. Output current | 1.5 - 3 A/phase
Drive type | Double-pole const. PWM
Compatible Stepper motors | 4/6/8 leads

Table 2: TB6560 Data sheet

### 5.2 Power supply

As we are suppplying our motor with 12V, the calculation of the power consumption will be like this:

Total power Pt = External Control Unit Pe + Motor Pm | (1)
Pm = Io × Ui = 3A × 12V = 36W | (2)
Pm Pe ,so Pm ≈ Pt | (3)

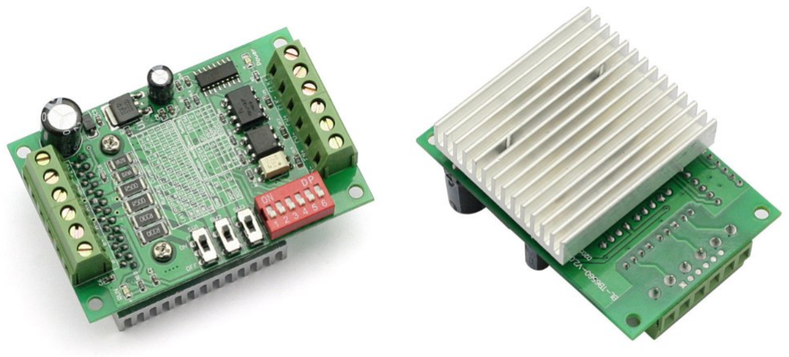
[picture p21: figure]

Figure 6: TB6560 Stepper Motor Driver Module

Our power supply must able to supply at least 40 Watts of power to drive our converying belt and control units.

### 5.3 Overall circuit

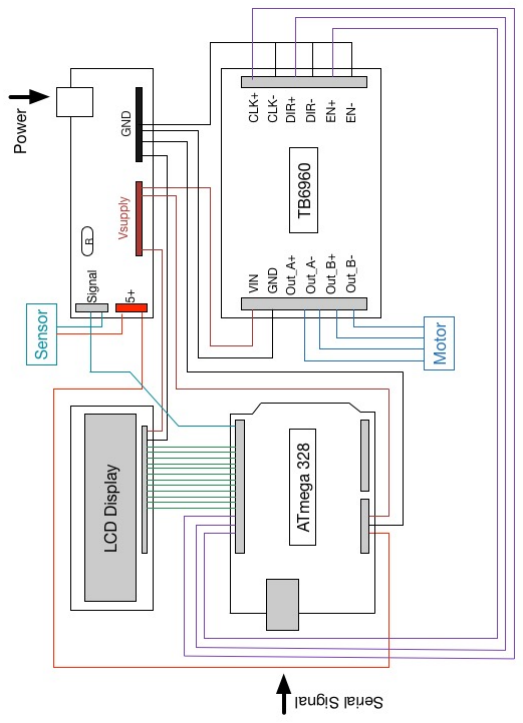
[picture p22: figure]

Figure 7: External Control Unit: cabling

## 6 Software - Ecu

### 6.1 Logical equivalence

The system logic of the external motor controller has 3 main states: initial, processing and waiting process:


Figure 8: Software Logic

In the boot up phase, the system will first check if all the hardware is connected and reset the position automatically. It sends continuous signals to the motor to move the conveying base back to the origin and if the base has a physical contact with it, the digital sensor will set its output to HIGH.

After the reboot, the system is ready and waits for the serial command from the andrix or PCs. The serial bandwidth has already been set in the initial process and the default is 9600bit/s. Any serial signal during the waiting phase will be stored in a String buffer to futher process. The conmunication will be base on the protocol from section 6.3.

### 6.2 Function description

To find more detail of a specific function, please go to section 6.4.

Name | Use | Input | Return
setup() loop() serialEvent() reset() goToPosition() lcdShow() lcdBackLightOnOff() | Init Setup Main loop Reading Serial Input and buffer them Reset position to origin Go to position Display message on LCD Display Turn LCD Light On or Off | — — — — Integer String 1,2 boolean | — depend — — — — —

### 6.3 Communication protocol

Command ...@ | Description @ - end; ... - Commands | Sample Bandwith = 9600 bit/sec
ENA@ DIS@ RES@ GTP...@ SST...@ CTP@ CTS@ LED...@ | Enable the motor Disable the motor Reset, back to origin Go to xxx/10 mm position [Max. 4950] Set delay of motor(default 0) [2 byte] send back to the current position [2 byte] send back the current speed(delay) [2 byte] Turn LED Display light ON or Off | Send: ENA@ – Motor enabled Send: DIS@ – Motor disabled Send: RES@ – Axis back to 0 position Send: GTP1234@ – Axis go to 123.4mm Send: SST1@ – Set 1 ms delay for each step Send: CTP@;Return: 123@ – Current Position Send: CTS@;Return: 1@ – Current Delay Send: LED1@–Light turn On

Table 3: Protocol: Stepper Motor Control

If you want to modify the setting of the communication bandwidth, you will have to programme the external control unit with the source code from 6.4 using Arduino IDE.

Communication sample:

1 Normal Ope r a ti on :
2 1 .SEND: | ENA@ | \\Enable s the motor
3 2 .SEND: | GTP1000@ | \\Go t o P o si ti o n 10cm
4 3 .SEND: | RES@ | \\ Rese t p o s i t i o n t o 0 , a l l d e f a u l t v al u e
5
6
7 Move Sl owl y :
8 1 .SEND: | ENA@ | \\Enable s the motor
9 2 .SEND: | SST1@ | \\ Se t Delay f o r 1ms
10 3 .SEND: | GTP500@ | \\ C onv ayin gbel t w i l l move sl o wl y t o 5cm
11
12
13 Let c onvey o r b e l t t o be a bl e t o move by hand :
14 1 .SEND: | DIS@ | \\ Di s a bl e the motor
15 2 .SEND: | RES@ | \\WARNING: You must r e s e t the p o s i t i o n !
16
17
18 Turn On/ O f f LED Di s pl a y b a c kli g h t :
19 1 .SEND: | LED1@ | \\Turn On l i g h t
20 2 .SEND: | LED0@ | \\Turn O f f l i g h t
21 3 .SEND: | LED3@ | \\Turn On l i g h t (Any num.>0 w i l l be ’ON’ )

### 6.4 Source code

1 /∗
2 | Name : | S t e p p e r Motor C o n t r o l l e r ( S e r i a l Communication ) − 3 . 5A low power
3 | Autor : | Alexander Wurm, Kevin Pan
4 | D i s c r i b t i o n : | S t e p p e r Motor C o n t r o l l e r ( S e r i a l Communication ) − 3 . 5A low power
5 | L a s t Update : | 0 4 . 2 0 1 5
6 | Con tac t : | kpan@s tuden t . tgm . ac . a t , awurm@student . tgm . ac . a t
7 ∗/
8 #include <Li q ui d C r y s t al . h>
9 //Pin s e t u p s :
10 #def ine S e n s o r T o u c h S e n s o r Pi n 7 | //Touch Sensor ( i n i t ) p in
11 #def ine M o t o r Cl oc k pin 9 | // Clock ( Tacks ) CLK+ p in
12 #def ine M o t o r Di r e c ti o n pi n 8 | // D i r e c t i o n CW+ p in
13 #def ine M o t o r En able pin 10
14 #def ine Lcd D7 pin 2
15 #def ine Lcd D6 pin 3
16 #def ine Lcd D5 pin 4
17 #def ine Lcd D4 pin 5
18 #def ine Lcd En abl e pin 11 19 #def ine Lcd RS pin 12
20 #def ine L c d B a c kli g h t pi n 6
21
22 // S t a t i c v a l u e s :
23 #def ine Maximum steps 32250 | //Maximum s t e p s
24 #def ine A xi s l e n g t h 4950 | //Maximum Leng th
25 #def ine Cl o c k im p ul s 100 | // M icrosecond
26
27 // V a r i a b l e s :
28 int C u r r e n t p o si ti o n = 0 ; | // M il ime t e r
29 f l o a t S t e p r e s o l u t i o n = 0 . 1 5 3 4 9; | // S tepmo tor s t e p−r e s o l u t i o n in mm
30 S t ri n g i n p u t S t ri n g = ” ” ; | // a s t r i n g t o h ol d incom ing d a t a
31 b o ole an s t ri n gC om pl e t e = f a l s e ; | // w he t her t h e s t r i n g i s c om ple te
32 int delayO fMotor = 0 ;
33 b o ole an m o t o r e n a bl e ; | // Remembers t h e s t a t u s o f motor en / d i s a b l e
34 Li q ui d C r y s t al l c d Di s pl a y ( Lcd RS pin , Lcd En able pin , Lcd D4 pin , Lcd D5 pin , Lcd D6 pin , Lcd D7 pin ) ; 35
36 void se t up ( ) {
37 | //Lcd D i s pl ay s e t u p :
38 | l c d Di s pl a y . b e gi n ( 1 6 , 2 ) ;
39 | pinMode ( L c d B a c kli g h t pi n , OUTPUT) ;
40 | lcdBackLightOnO f f ( t r u e ) ;
41 | lcdShow ( ” System : S t a r ti n g ” , ” Pl e a s e Wait . . . ” ) ;
42
43 | // Re se rv i ng memory s p a c e s f o r in pu tS tre am :
44 | S e r i a l . b e gi n ( 9 6 0 0 ) ;
45 | i n p u t S t ri n g . r e s e r v e ( 3 2 ) ;
46
47 | //Motor p in Se tup :
48 | m o t o r e n a bl e=t r u e ;
49 | pinMode ( Mo to r Enable pin ,OUTPUT) ;
50 | pinMode ( M o t o r Di r e c ti o n pi n , OUTPUT) ;

51 | pinMode ( M o t o r Cl ock pin , OUTPUT) ;
52 | pinMode ( Sen s o r T ouch Sen s o r Pin , INPUT ) ;
53 | d i g i t a lW r i t e ( Mo to r Enable pin ,LOW) ;
54 | d i g i t a lW r i t e ( M o t o r Di r e c ti o n pi n , LOW) ;
55 | d i g i t a lW r i t e ( M o t o r Cl ock pin , LOW) ;
56 | d el a y ( 2 0 0 0 ) ;
57
58 | // S t a r t R e s e t i n g P o s i t i o n :
59 | lcdShow ( ” R e s e ti n g | POS. ” , ” Pl e a s e Wait . . . ” ) ;
60 | d el a y ( 2 0 0 0 ) ;
61 | r e s e t ( ) ;
62
63 | // F i n i s h R e s e t i n g P o s i t i o n :
64 | lcdShow ( ” R e s e ti n g | POS . . . ” , ” Fi ni s h e d . . . ” ) ;
65 | d i g i t a lW r i t e ( Mo to r Enable pin ,HIGH ) ;
66 | m o t o r e n a bl e= f a l s e ;
67 | d el a y ( 1 0 0 0 ) ;
68 | lcdShow ( ”Waiting Command” , ” POS” ) ;
69 }
70
71 void s e r i a l E v e n t ( ) {
72 | while ( S e r i a l . a v a i l a b l e ( ) ) {
73 | // g e t t h e new b y t e :
74 | char inChar = ( char ) S e r i a l . re ad ( ) ;
75 | // add i t t o t h e i n p u t S t r i n g :
76 | i n p u t S t ri n g += inChar ;
77 | // i f t h e incom ing c h a r a c t e r i s a newl ine , s e t a f l a g
78 | // so t h e main l o o p can do s ome t h ing ab o u t i t :
79 | i f ( inChar == ’@’ ) {
80 | s t ri n gC om pl e t e = t r u e ;
81 | }
82 | }
83 }
84
85 void l o o p ( ) {
86 | i f ( s t ri n gC om pl e t e ) {
87 | S t ri n g command=i n p u t S t ri n g . s u b s t ri n g ( 0 , 3 ) ;
88 | S t ri n g showCommand=”Command: ”+command ;
89 | lcdShow ( showCommand , ” POS” ) ;
90 | i f (command==”ENA” ){
91 | // S e r i a l . p r i n t l n (” motor e n a bl e d ” ) ;
92 | d i g i t a lW r i t e ( Mo to r Enable pin , LOW) ;
93 | m o t o r e n a bl e=t r u e ;
94 | }
95 | e l s e i f (command==”DIS” ){
96 | // S e r i a l . p r i n t l n (” motor d i s a b l e d ” ) ;
97 | d i g i t a lW r i t e ( Mo to r Enable pin ,HIGH ) ;
98 | m o t o r e n a bl e= f a l s e ;
99 | }
100 | e l s e i f (command==”RES” ){
101 | // S e r i a l . p r i n t l n (” P o s i t i o n r e s e t s ” ) ;

r e s e t ( ) ;
}
e l s e i f (command==”GTP” ){
int pos=i n p u t S t ri n g . s u b s t ri n g ( 3 , i n p u t S t ri n g . l e n g t h ( ) ) . t o I n t ( ) ; // S e r i a l . p r i n t (” Going t o p o s i t i o n : \ t ” ) ; S e r i a l . p r i n t l n ( pos ) ;
g oT oP o si ti on ( pos ) ;
}
e l s e i f (command==”SST” ){
int d el=i n p u t S t ri n g . s u b s t ri n g ( 3 , i n p u t S t ri n g . l e n g t h ( ) ) . t o I n t ( ) ; // S e r i a l . p r i n t (” Se t d e l a y t o : \ t ” ) ; S e r i a l . p r i n t l n ( d e l ) ;
delayO fMotor=d el ;
}
e l s e i f (command==”CTP” ){
S t ri n g out = S t ri n g ( C u r r e n t p o si ti o n ) + ”@” ; S e r i a l . p r i n t l n ( out ) ;
}
e l s e i f (command==”CTS” ){
i f ( delayO fMotor==0){
S e r i a l . p r i n t l n ( ” 0@” ) ;
}
e l s e {
S t ri n g out = S t ri n g ( delayO fMotor ) + ”@” ; S e r i a l . p r i n t l n ( out ) ;
}
}
e l s e i f (command==”LED” ){
b o ole an o n o f f = i n p u t S t ri n g . s u b s t r i n g ( 3 , i n p u t S t ri n g . l e n g t h ( ) ) . t o I n t ( ) ; lcdBackLightOnO f f ( o n o f f ) ;
}
e l s e {
// S e r i a l . p r i n t l n (”SYSTEM: S e r i a l i n p u t e r r o r ” ) ; // S e r i a l . p r i n t (” In p u t : \ t ” ) ;
// S e r i a l . p r i n t l n ( i n p u t S t r i n g ) ;
}

lcdShow ( showCommand , ” POS” ) ;
// c l e a r t h e s t r i n g :
i n p u t S t ri n g = ” ” ;
s t ri n gC om pl e t e = f a l s e ;
}
142 }
144 void r e s e t ( ) { | //RESET THE POSITION BACK TO 0 USING SENSOR
i f ( m o t o r e n a bl e==t r u e ){
d i g i t a lW r i t e ( M o t o r Di r e c ti o n pi n , HIGH ) ;
while ( ! di gi t al R e a d ( S e n s o r T o u c h S e n s o r Pi n ) ) { d i g i t a lW r i t e ( M o t o r Cl ock pin , HIGH ) ;
d el a yMi c r o s e c o n d s ( Cl o c k im p ul s ) ;
d i g i t a lW r i t e ( M o t o r Cl ock pin , LOW) ;
d el a yMi c r o s e c o n d s ( Cl o c k im p ul s ) ;
d el a y ( delayO fMotor ) ;

153 | }
154 | C u r r e n t p o si ti o n = 0 ;
155 | }
156 }
157
158 void g oT oP o si ti on ( int x p o s i t i o n ){
159 | i f ( m o t o r e n a bl e==f a l s e ){ return ; }
160
161 | // c h e c k i n g i f t h e i n p u t v a l u e i s p o s i b l e :
162 | i f ( x p o s i t i o n <0 | | x p o s i t i o n >4950){
163 | return ;
164 | }
165
166 | // c a l c u l a t i n g t h e d i f f e r e n c e :
167 | int d i f f = x p o s i t i o n − C u r r e n t p o si ti o n ;
168 | i f ( d i f f >0){
169 | d i g i t a lW r i t e ( M o t o r Di r e c ti o n pi n , LOW) ;
170 | }
171 | e l s e i f ( d i f f <0){
172 | d i g i t a lW r i t e ( M o t o r Di r e c ti o n pi n , HIGH ) ;
173 | d i f f=−d i f f ;
174 | }
175 | e l s e {
176 | return ;
177 | }
178
179 | // I f t h e p o s i t i o n i s g o i n g back t o z e r o : ( w i l l be r e p a l c e d w i t h a d i g i t a l b u t t o n )
180 | i f ( x p o s i t i o n ==0){
181 | int k = ( int ) ( C u r r e n t p o si ti o n / S t e p r e s o l u t i o n ) ;
182 | for ( int i =1; i<=k ; i ++){
183 | d i g i t a lW r i t e ( M o t o r Cl ock pin , HIGH ) ;
184 | d el a yMi c r o s e c o n d s ( Cl o c k im p ul s ) ;
185 | d i g i t a lW r i t e ( M o t o r Cl ock pin , LOW) ;
186 | d el a yMi c r o s e c o n d s ( Cl o c k im p ul s ) ;
187 | d el a y ( delayO fMotor ) ;
188 | }
189 | C u r r e n t p o si ti o n =0;
190 | return ;
191 | }
192
193 | int s t e p s = ( int ) ( d i f f / S t e p r e s o l u t i o n ) ;
194 | for ( int i =1; i<=s t e p s ; i ++){
195 | d i g i t a lW r i t e ( M o t o r Cl ock pin , HIGH ) ;
196 | d el a yMi c r o s e c o n d s ( Cl o c k im p ul s ) ;
197 | d i g i t a lW r i t e ( M o t o r Cl ock pin , LOW) ;
198 | d el a yMi c r o s e c o n d s ( Cl o c k im p ul s ) ;
199 | d el a y ( delayO fMotor ) ;
200 | }
201 | C u r r e n t p o si ti o n = x p o s i t i o n ;
202 }
203

204 void lcdShow ( S t ri n g o u t p u t S t ri n g 1 , S t ri n g o u t p u t S t ri n g 2 ) {
205 | // Cle an ing t h e s c r e e n :
206 | l c d Di s pl a y . c l e a r ( ) ;
207
208 | // F i r s t row :
209 | l c d Di s pl a y . s e t C u r s o r ( 0 , 0 ) ;
210 | l c d Di s pl a y . p r i n t ( o u t p u t S t ri n g 1 ) ;
211
212 | // Second Row :
213 | l c d Di s pl a y . s e t C u r s o r ( 0 , 1 ) ;
214 | i f ( o u t p u t S t ri n g 2 == ” POS” ){
215 | S t ri n g out ;
216 | out = ”POS: ” + S t ri n g ( C u r r e n t p o si ti o n ) ;
217 | out = out + ” mm” ;
218 | l c d Di s pl a y . p r i n t ( out ) ;
219 | }
220 | e l s e {
221 | l c d Di s pl a y . p r i n t ( o u t p u t S t ri n g 2 ) ;
222 | }
223 }
224
225 void lcdBackLightOnO f f ( b o ole an a ){
226 | i f ( a==t r u e ){ d i g i t a lW r i t e ( L c d B a c kli g h t pi n ,HIGH ) ; }
227 | e l s e i f ( a==f a l s e ){ d i g i t a lW r i t e ( L c d B a c kli g h t pi n ,LOW) ; }
228 }

## Part III

# Conclution

After assembling the mechanical design and putting all electronic components together, we devised a very simple system. We tested the axis accuracy and it is much more percise than we first expected.

## 7 Resaults and Comparison

In comparison with some of the industrial standard machines, our solution can be up to 10 times cheaper. Of course, the standard system can control/supply multiple linear or even other kinds of axises at the same time. But one of the biggest advantages of distributed system is flexibility.

Unter the same kind of hardware structure, we are able to connect multiple controllers with a central computer, and control them induvidually. It is also even posible to implement some kind of smart algorithm, which is designed spicificly for each individual enviroment.

In this example we only show one way of using an Andrix controller in Industrial area. It shows us the potential of distributed system and can be one of the most important keys for ’Industrial 4.0’. It will change the way we look at the normal rigid structure.

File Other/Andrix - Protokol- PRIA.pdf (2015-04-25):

Was ist Andrix?
Vorteile?
Unsere Idee mit Andrix Industrie? Concept plan

Arbeitsschritte
Unterschiede zwischen 2 motoren/Achsen Wir nehmen NEMA 23 als Beispiel

Achse:
Model nummer
länge/breite/gröse
beschränkungen zu beachten Datenblatt (falls es gibt)
CAD Zeichnung

Motor:
Gröse, Stärke
Drehmoment
Maximale Drehzahl
Datenblatt
CAD Zeichung

Wellenadapter:
Warum brauchen wir es? Problem beschreibung Meterial Auswall
Messungen

# Andrix - Protokol: PRIA

## About PRIA(Wurm)[1]

## Team(Wurm)[1]

## Concepte(PAN)[2]

## Umsetzung(PAN)[1]

## Mechanic(PAN)[3,4]

CAD Zeichnung

Gesamt:
Messungen
CAD Zeichnung

Fotos von end produkten

Andrix:
External Motor Steuerung:
Welche leistung hat der motor?
Welche leistung muss diese Krontroller treiben können? Steuerungsverlauf
Bild
Beschreibung

Power supply
Interne Schaltungs plan (friztzing oder co.)

Fotos von end produkten

Control bzw. Logische Verlauf
Funktion beschreibung
Source Code mit genaue Commendar dazu

Testergebnisse: Gut? Schlecht?
Vergleich mit Industrie Standard Steuerung: Preis
Flexibilität
Erweiterungsmöglichkeit(Open Source?) Größe

Idee mit Industrie 3.0 zusammen verbinden

## Electronik(Wurm)[3]

## Software(Wurm)[3,4]

## Conclutions(PAN)[2]

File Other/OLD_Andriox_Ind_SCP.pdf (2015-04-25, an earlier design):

# STEPPER-MOTOR CONTROL PROTOCOL

Command | Description | Sample
….@ | @ - end ; … - commands | Bandwith = 9600
ENA@ | Enable the Motor | Send: ENA@ —— motor enabled
DIS@ | Disable the Motor | Send: DIS@ —— motor disabled
RES@ | Reset ( back to origin ) | Send: RES@ —— Axis back to 0 position
GTP….@ | Go To xxxx mm position [Max=4950] | Send: GTP1234@ —— Axis go to 1234 mm Position
SST….@ | Set delay of motor (default: 0) [2 byte] | Send: SST0@ —— Set delay of motor 0 ms
CTP@ | send back the current position (2 byte) : xxxx | Send: CTP@ —— Return: “2341@” (current position 2341mm)
CTS@ | send back the current speed (2 byte) : xxxx | Send: CTS@ —— Return: “450@” (current speed 450)

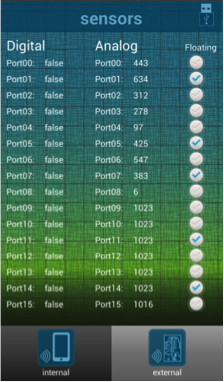
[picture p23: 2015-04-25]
LaTex-Documentation/img/andrix-sensors.png

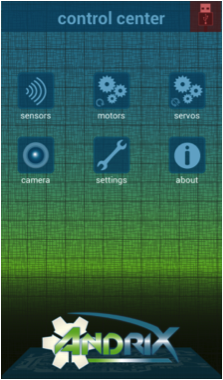
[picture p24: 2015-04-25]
LaTex-Documentation/img/andrix-controlcenter.png

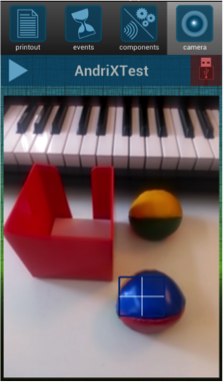
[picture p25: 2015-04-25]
Other/img/andrix-camera.png

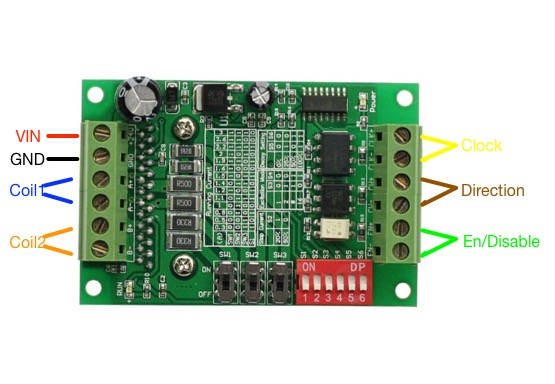
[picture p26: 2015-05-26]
LaTex-Documentation/img/TB6560-pin.jpg

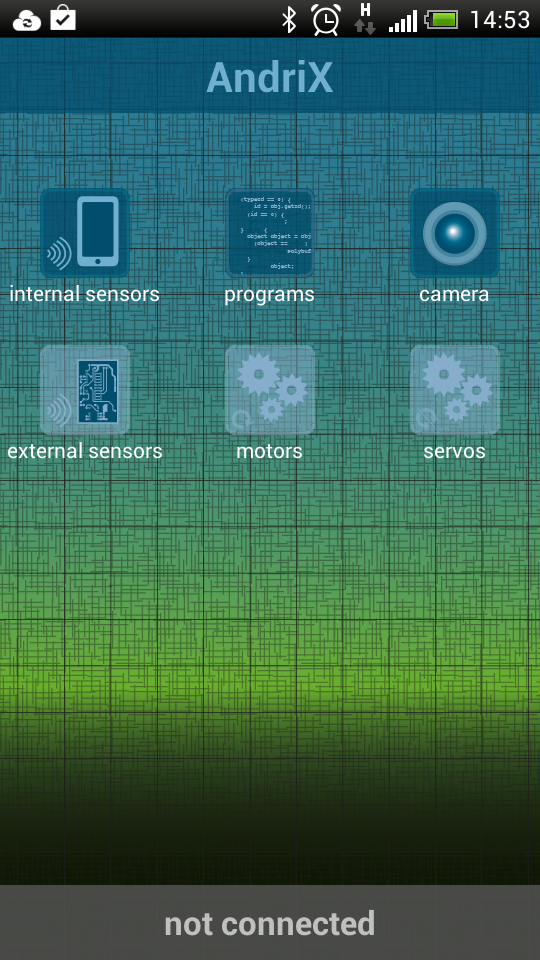
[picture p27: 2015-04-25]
Other/img/andrix-cc-new.png

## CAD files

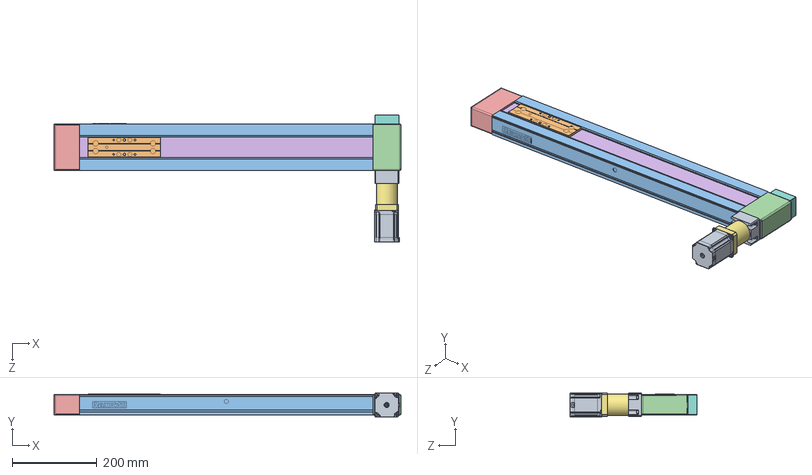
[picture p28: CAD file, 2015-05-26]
LaTex-Documentation/cad/CAD_Assembly.SLDASM
816.5 x 56.4 x 299.2 mm
Stepper motor NEMA 23HS7430
CKR_110_NN_1_69_TT
CKR_110_NN_1_69_HK
CKR_110_NN_1_69_AK
CKR_110_NN_1_69_SK
CKR_110_NN_1_69_RIEM
R039612056
R037144005
R039601214

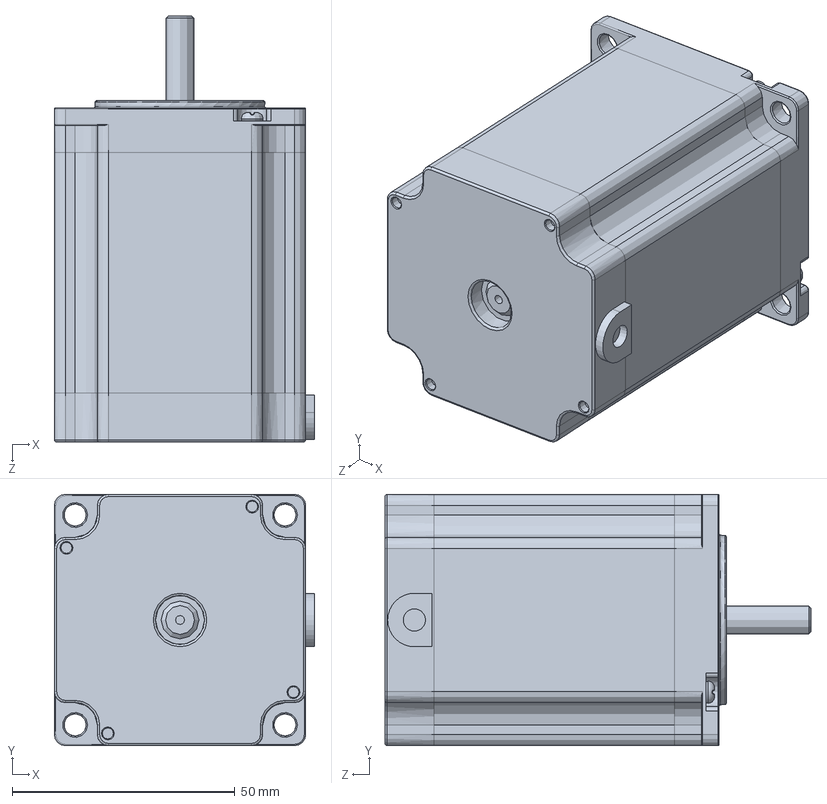
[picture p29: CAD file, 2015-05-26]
LaTex-Documentation/cad/NEMA23/Stepper motor NEMA 23HS7430.SLDPRT
58.4 x 56.4 x 95.6 mm

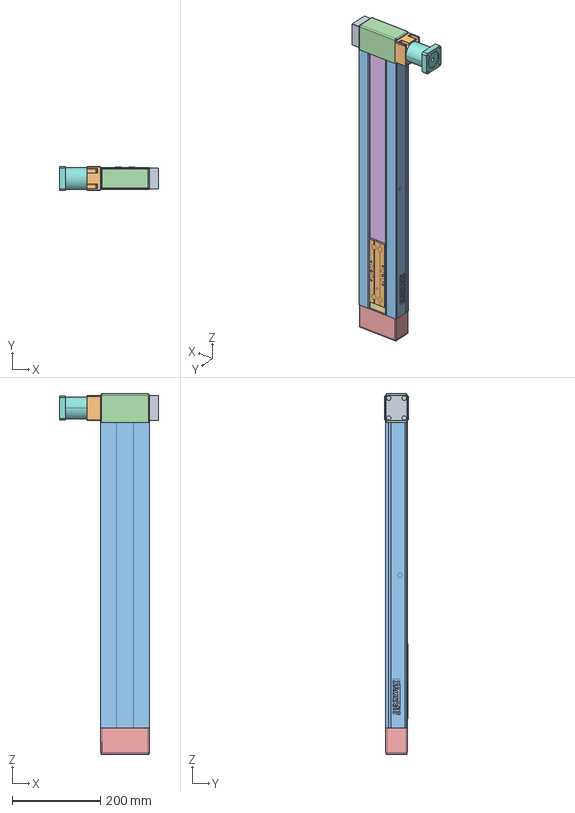
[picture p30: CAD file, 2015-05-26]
LaTex-Documentation/cad/Conveyingbelt_cad/CKR_110_NN_1_69.stp
224.5 x 55.0 x 816.5 mm
CKR_110_NN_1_69_SKEL
CKR_110_NN_1_69_TT
CKR_110_NN_1_69_HK
CKR_110_NN_1_69_AK
CKR_110_NN_1_69_SK
CKR_110_NN_1_69_RIEM
R039612056
R037144005
R039601214

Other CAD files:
LaTex-Documentation/cad/Conveyingbelt_cad/CKR_110_NN_1_69_AK.sldprt
LaTex-Documentation/cad/Conveyingbelt_cad/CKR_110_NN_1_69_TT.sldprt
LaTex-Documentation/cad/Conveyingbelt_cad/CKR_110_NN_1_69_SK.sldprt
LaTex-Documentation/cad/Conveyingbelt_cad/CKR_110_NN_1_69_RIEM.sldprt
LaTex-Documentation/cad/Conveyingbelt_cad/CKR_110_NN_1_69_HK.sldprt
LaTex-Documentation/cad/Conveyingbelt_cad/R039612056.sldprt
LaTex-Documentation/cad/Conveyingbelt_cad/R039601214.sldprt
LaTex-Documentation/cad/Conveyingbelt_cad/R037144005.sldprt
LaTex-Documentation/cad/CAD_Assembly.SLDDRW
LaTex-Documentation/cad/CKR_110_NN_1_69.SLDDRW
LaTex-Documentation/cad/Conveyingbelt_cad/CKR_110_NN_1_69.SLDASM
LaTex-Documentation/cad/Stepper motor NEMA 23HS7430.SLDDRW

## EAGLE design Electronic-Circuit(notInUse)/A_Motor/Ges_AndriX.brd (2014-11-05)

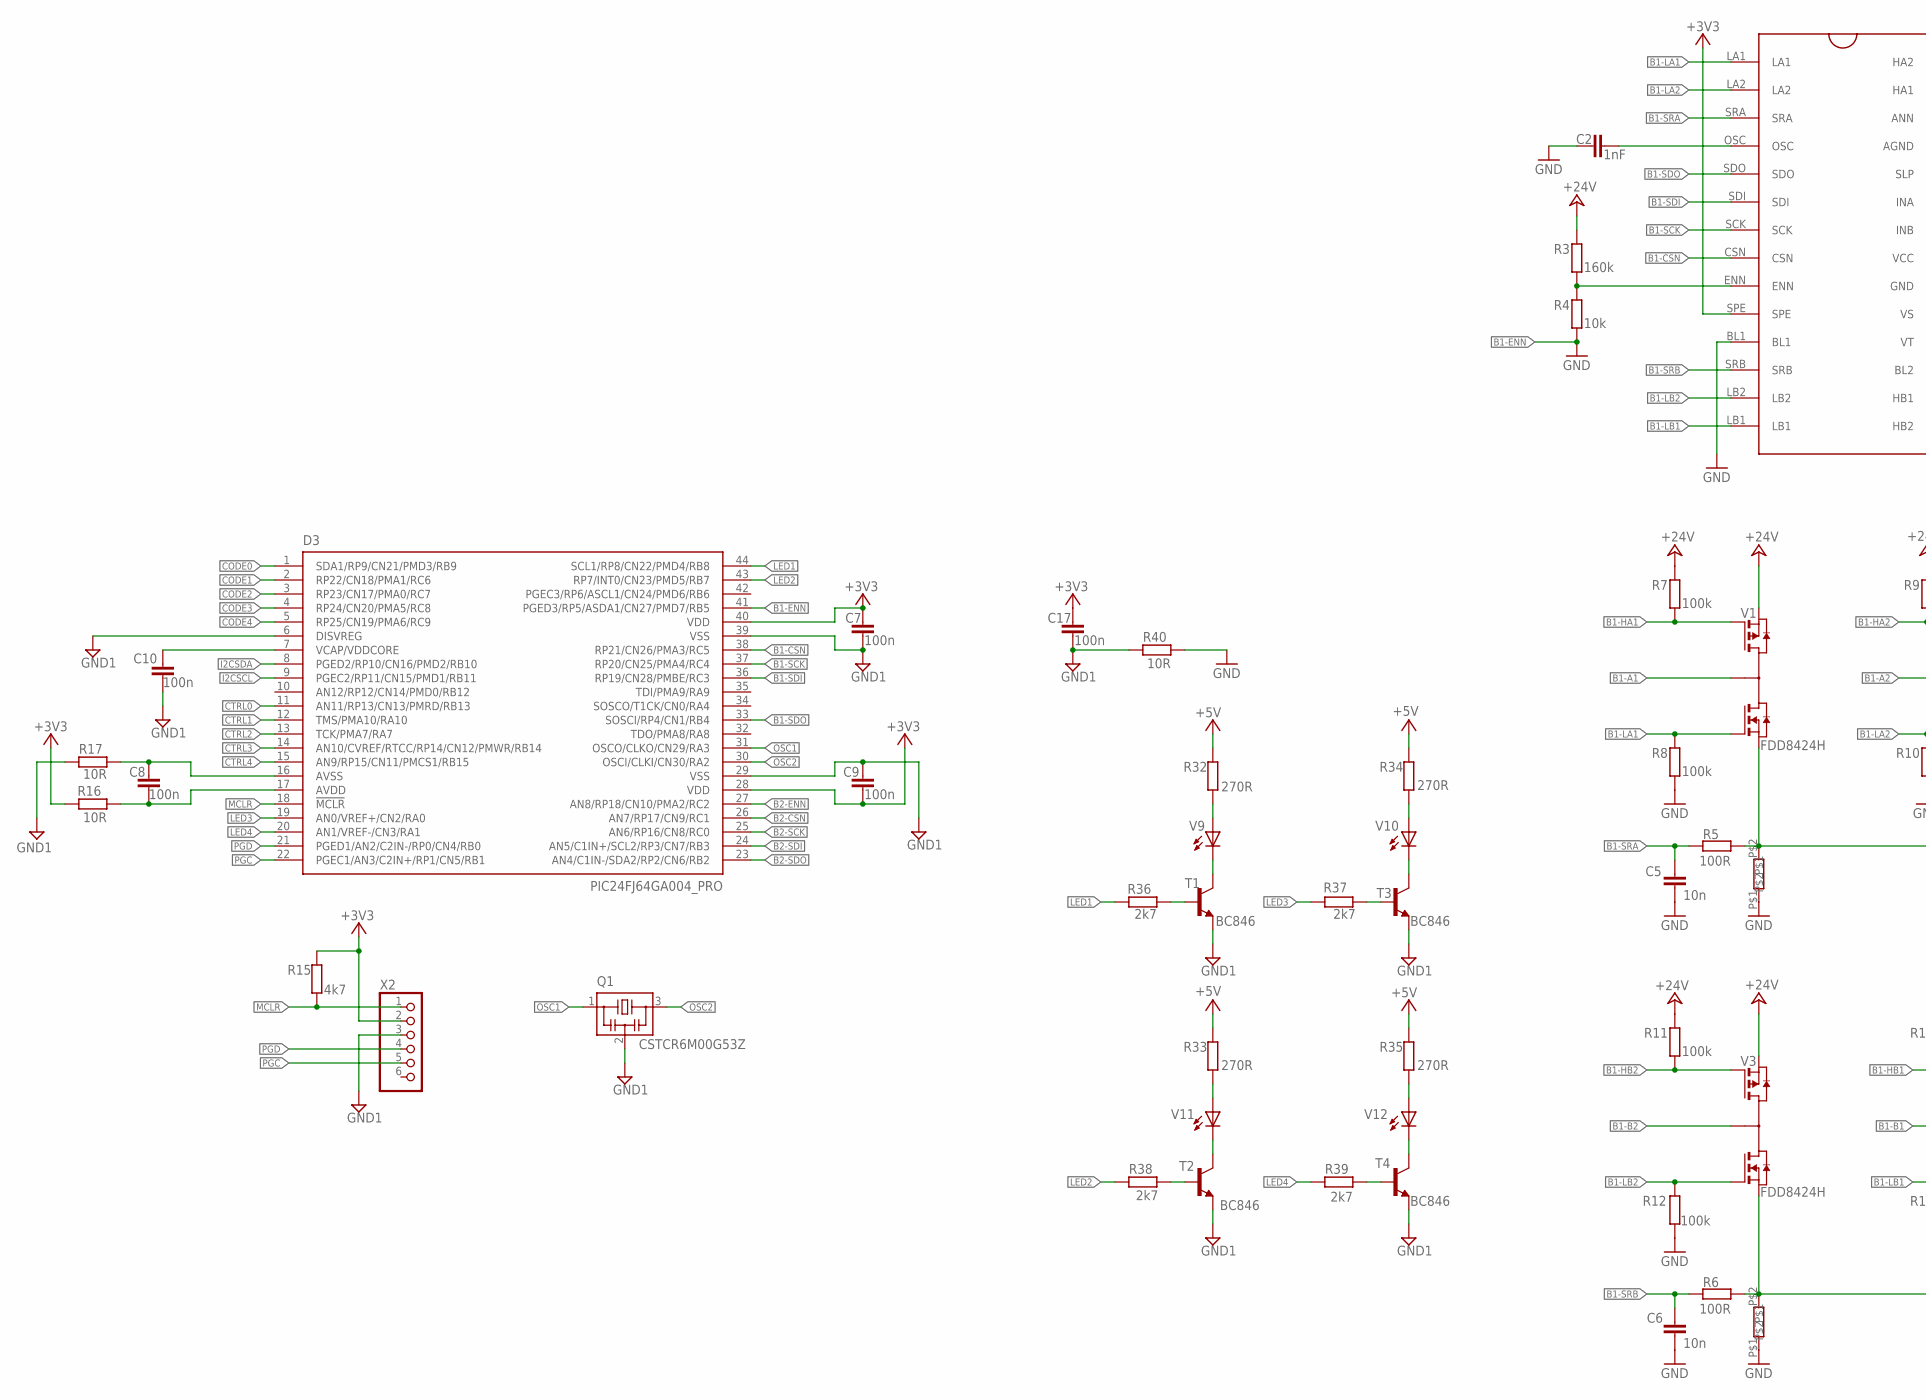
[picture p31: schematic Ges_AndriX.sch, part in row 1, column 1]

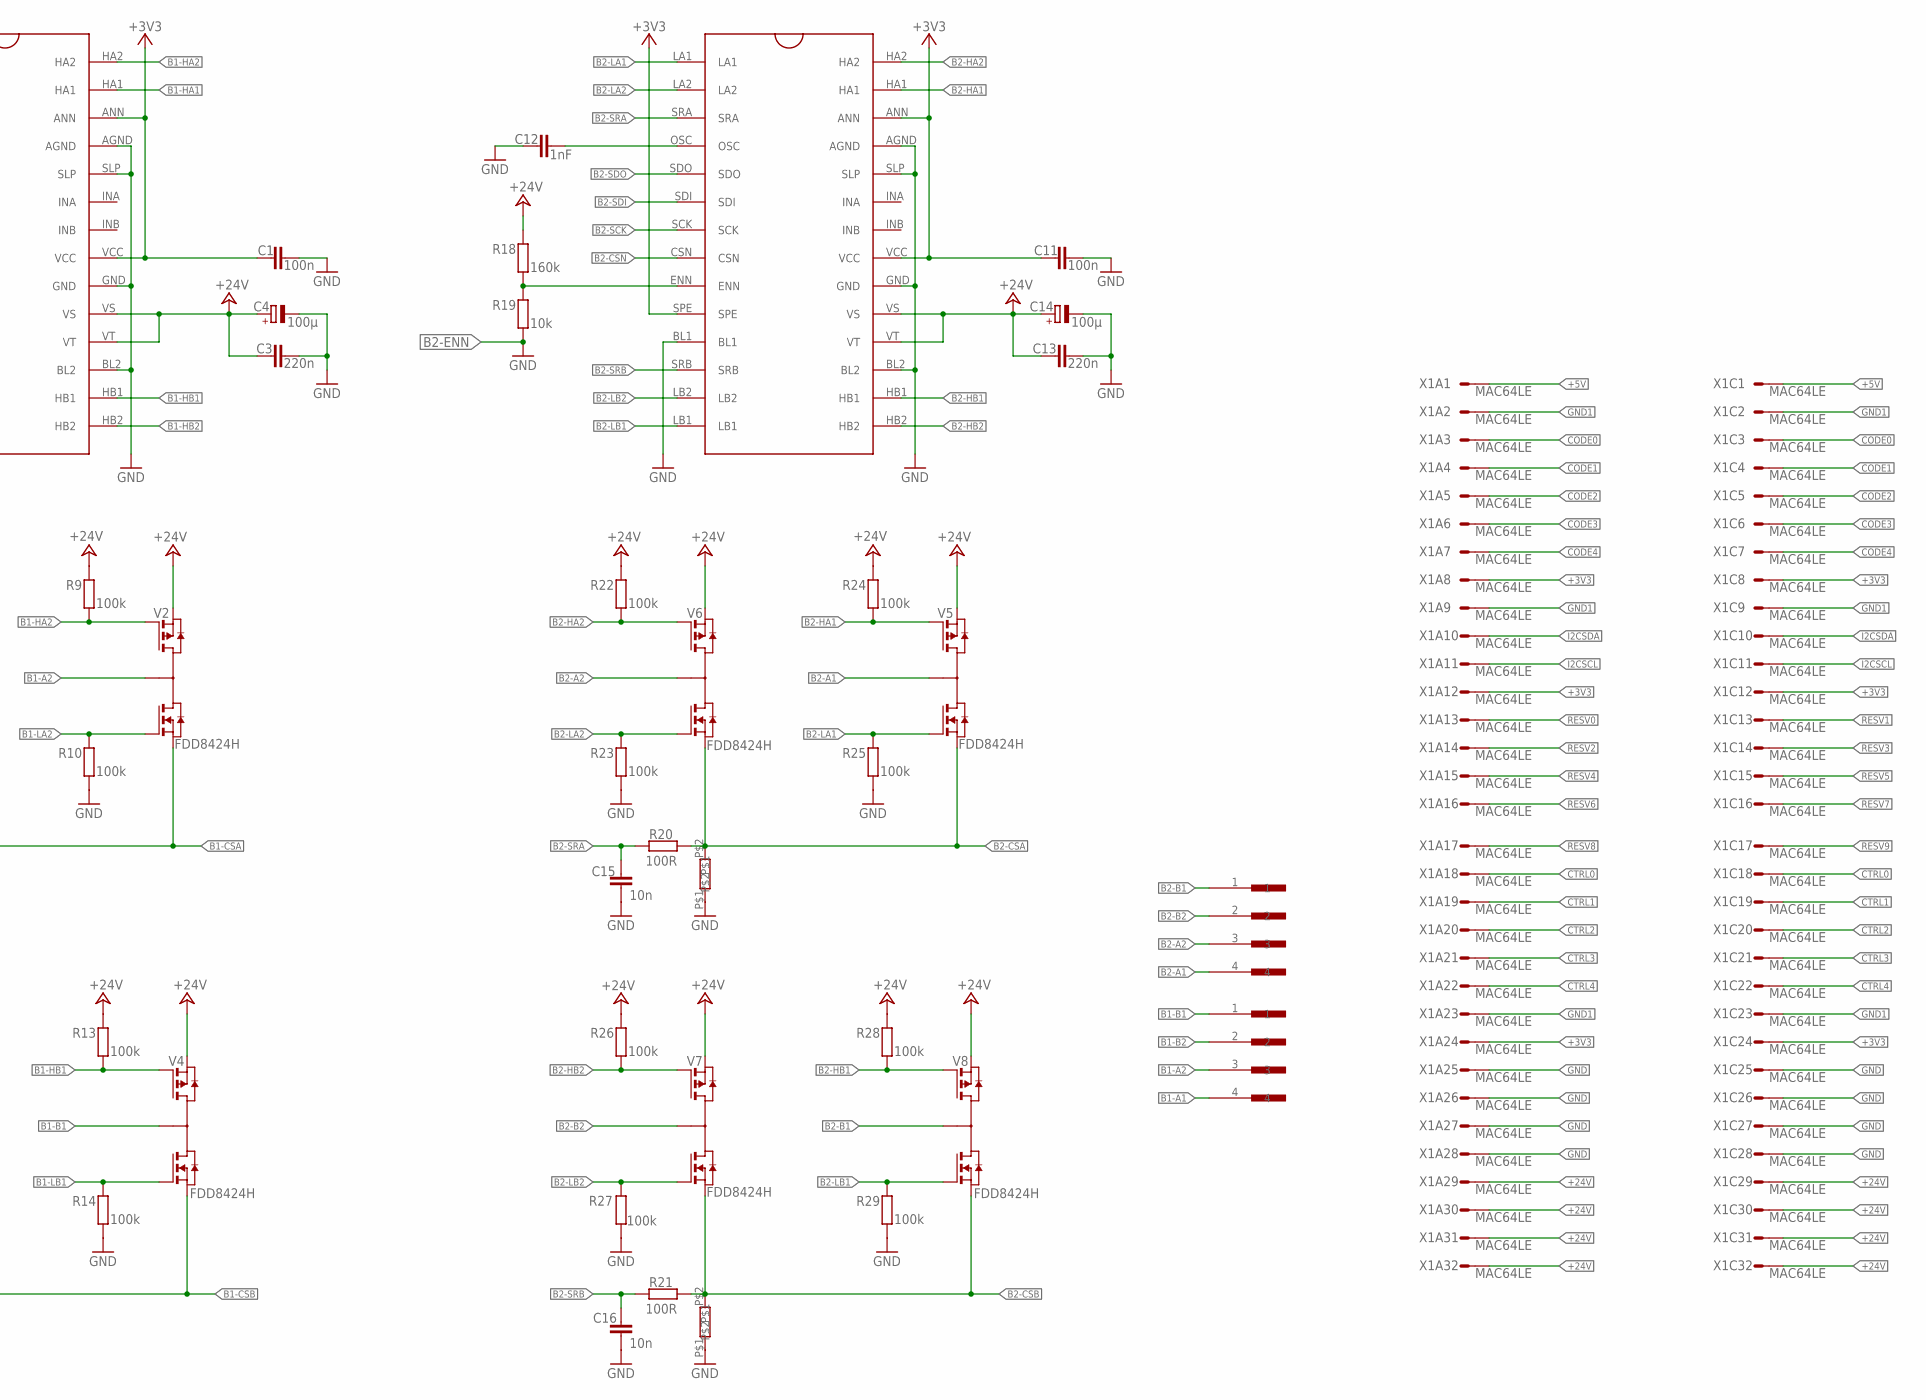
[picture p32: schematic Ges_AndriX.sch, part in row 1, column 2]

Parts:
C1, C11: 100n; C1206
C2, C12: 1nF; C1206
C3, C13: 220n; C1206
C4, C14: 100µ; 140CLH-1010
C5, C6, C15, C16: 10n; C1206
C7, C8, C9, C10, C17: 100n; C1206K
D1, D2: TMC249; SO28
D3: PIC24FJ64GA004_PRO; TQFP44
Q1: CSTCR6M00G53Z; CSTER12M
R1, R2, R30, R31: 30m; RS
R3, R18: 160k; M1206
R4, R19: 10k; M1206
R5, R6, R20, R21: 100R; M1206
R7, R8, R9, R10, R11, R12, R13, R14, R22, R23, R24, R25, R26, R27, R28, R29: 100k; R1206
R15: 4k7; M1206
R16, R17, R40: 10R; M1206
R32, R33, R34, R35: 270R; M1206
R36, R37, R38, R39: 2k7; M1206
T1, T2, T3, T4: BC846; SOT23
V1, V2, V3, V4, V5, V6, V7, V8: FDD8424H; TO-252-4L
V9, V10, V11, V12: LEDCHIPLED_1206; CHIPLED_1206
X1: MAC64LE; MAC64L
X2: PINHD-1X6; 1X06
X3, X4: X_4POL

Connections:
+3V3: C1.1, C7.2, C9.2, C11.1, C17.2, D1.ANN, D1.SPE, D1.VCC, D2.ANN, D2.SPE, D2.VCC, D3.28 (VDD), D3.40 (VDD), R15.2, R16.2, X1.A8, X1.A12, X1.A24, X1.C8, X1.C12, X1.C24, X2.2
+5V: R32.2, R33.2, R34.2, R35.2, X1.A1, X1.C1
+24V: C3.1, C4.+, C13.1, C14.+, D1.VS, D1.VT, D2.VS, D2.VT, R3.2, R7.2, R9.2, R11.2, R13.2, R18.2, R22.2, R24.2, R26.2, R28.2, V1.S2, V2.S2, V3.S2, V4.S2, V5.S2, V6.S2, V7.S2, V8.S2, X1.A29, X1.A30, X1.A31, X1.A32, X1.C29, X1.C30, X1.C31, X1.C32
B1-A1: V1.D1D2, X4.4
B1-A2: V2.D1D2, X4.3
B1-B1: V4.D1D2, X4.1
B1-B2: V3.D1D2, X4.2
B1-CSA: R2.P$2, R5.2, V1.S1, V2.S1
B1-CSB: R1.P$2, R6.2, V3.S1, V4.S1
B1-CSN: D2.CSN, D3.38 (RP21/CN26/PMA3/RC5)
B1-ENN: D3.41 (PGED3/RP5/ASDA1/CN27/PMD7/RB5), R4.1
B1-HA1: D2.HA1, R7.1, V1.G2
B1-HA2: D2.HA2, R9.1, V2.G2
B1-HB1: D2.HB1, R13.1, V4.G2
B1-HB2: D2.HB2, R11.1, V3.G2
B1-LA1: D2.LA1, R8.2, V1.G1
B1-LA2: D2.LA2, R10.2, V2.G1
B1-LB1: D2.LB1, R14.2, V4.G1
B1-LB2: D2.LB2, R12.2, V3.G1
B1-SCK: D2.SCK, D3.37 (RP20/CN25/PMA4/RC4)
B1-SDI: D2.SDI, D3.36 (RP19/CN28/PMBE/RC3)
B1-SDO: D2.SDO, D3.33 (SOSCI/RP4/CN1/RB4)
B1-SRA: C5.1, D2.SRA, R5.1
B1-SRB: C6.1, D2.SRB, R6.1
B2-A1: V5.D1D2, X3.4
B2-A2: V6.D1D2, X3.3
B2-B1: V8.D1D2, X3.1
B2-B2: V7.D1D2, X3.2
B2-CSA: R20.2, R30.P$2, V5.S1, V6.S1
B2-CSB: R21.2, R31.P$2, V7.S1, V8.S1
B2-CSN: D1.CSN, D3.26 (AN7/RP17/CN9/RC1)
B2-ENN: D3.27 (AN8/RP18/CN10/PMA2/RC2), R19.1
B2-HA1: D1.HA1, R24.1, V5.G2
B2-HA2: D1.HA2, R22.1, V6.G2
B2-HB1: D1.HB1, R28.1, V8.G2
B2-HB2: D1.HB2, R26.1, V7.G2
B2-LA1: D1.LA1, R25.2, V5.G1
B2-LA2: D1.LA2, R23.2, V6.G1
B2-LB1: D1.LB1, R29.2, V8.G1
B2-LB2: D1.LB2, R27.2, V7.G1
B2-SCK: D1.SCK, D3.25 (AN6/RP16/CN8/RC0)
B2-SDI: D1.SDI, D3.24 (AN5/C1IN+/SCL2/RP3/CN7/RB3)
B2-SDO: D1.SDO, D3.23 (AN4/C1IN-/SDA2/RP2/CN6/RB2)
B2-SRA: C15.1, D1.SRA, R20.1
B2-SRB: C16.1, D1.SRB, R21.1
CODE0: D3.1 (SDA1/RP9/CN21/PMD3/RB9), X1.A3, X1.C3
CODE1: D3.2 (RP22/CN18/PMA1/RC6), X1.A4, X1.C4
CODE2: D3.3 (RP23/CN17/PMA0/RC7), X1.A5, X1.C5
CODE3: D3.4 (RP24/CN20/PMA5/RC8), X1.A6, X1.C6
CODE4: D3.5 (RP25/CN19/PMA6/RC9), X1.A7, X1.C7
CTRL0: D3.11 (AN11/RP13/CN13/PMRD/RB13), X1.A18, X1.C18
CTRL1: D3.12 (TMS/PMA10/RA10), X1.A19, X1.C19
CTRL2: D3.13 (TCK/PMA7/RA7), X1.A20, X1.C20
CTRL3: D3.14 (AN10/CVREF/RTCC/RP14/CN12/PMWR/RB14), X1.A21, X1.C21
CTRL4: D3.15 (AN9/RP15/CN11/PMCS1/RB15), X1.A22, X1.C22
GND: C1.2, C2.2, C3.2, C4.-, C5.2, C6.2, C11.2, C12.2, C13.2, C14.-, C15.2, C16.2, D1.AGND, D1.BL1, D1.BL2, D1.GND, D1.SLP, D2.AGND, D2.BL1, D2.BL2, D2.GND, D2.SLP, R1.P$1, R2.P$1, R8.1, R10.1, R12.1, R14.1, R23.1, R25.1, R27.1, R29.1, R30.P$1, R31.P$1, R40.1, X1.A25, X1.A26, X1.A27, X1.A28, X1.C25, X1.C26, X1.C27, X1.C28
GND1: C7.1, C9.1, C10.2, C17.1, D3.6 (DISVREG), D3.29 (VSS), D3.39 (VSS), Q1.2, R17.2, R40.2, T1.2 (E), T2.2 (E), T3.2 (E), T4.2 (E), X1.A2, X1.A9, X1.A23, X1.C2, X1.C9, X1.C23, X2.3
I2CSCL: D3.9 (PGEC2/RP11/CN15/PMD1/RB11), X1.A11, X1.C11
I2CSDA: D3.8 (PGED2/RP10/CN16/PMD2/RB10), X1.A10, X1.C10
LED1: D3.44 (SCL1/RP8/CN22/PMD4/RB8), R36.2
LED2: D3.43 (RP7/INT0/CN23/PMD5/RB7), R38.1
LED3: D3.19 (AN0/VREF+/CN2/RA0), R37.2
LED4: D3.20 (AN1/VREF-/CN3/RA1), R39.2
MCLR: D3.18 (!MCLR), R15.1, X2.1
unnamed: C2.1, D2.OSC
unnamed: C8.2, D3.17 (AVDD), R16.1
unnamed: C8.1, D3.16 (AVSS), R17.1
unnamed: C10.1, D3.7 (VCAP/VDDCORE)
unnamed: T1.3 (C), V9.C
unnamed: C12.1, D1.OSC
unnamed: T2.3 (C), V11.C
unnamed: T3.3 (C), V10.C
unnamed: D1.ENN, R18.1, R19.2
unnamed: T4.3 (C), V12.C
unnamed: R32.1, V9.A
unnamed: R33.1, V11.A
unnamed: R34.1, V10.A
unnamed: R35.1, V12.A
unnamed: R36.1, T1.1 (B)
unnamed: D2.ENN, R3.1, R4.2
unnamed: R37.1, T3.1 (B)
unnamed: R38.2, T2.1 (B)
unnamed: R39.1, T4.1 (B)
OSC1: D3.31 (OSCO/CLKO/CN29/RA3), Q1.1
OSC2: D3.30 (OSCI/CLKI/CN30/RA2), Q1.3
PGC: D3.22 (PGEC1/AN3/C2IN+/RP1/CN5/RB1), X2.5
PGD: D3.21 (PGED1/AN2/C2IN-/RP0/CN4/RB0), X2.4
RESV0: X1.A13
RESV1: X1.C13
RESV2: X1.A14
RESV3: X1.C14
RESV4: X1.A15
RESV5: X1.C15
RESV6: X1.A16
RESV7: X1.C16
RESV8: X1.A17
RESV9: X1.C17

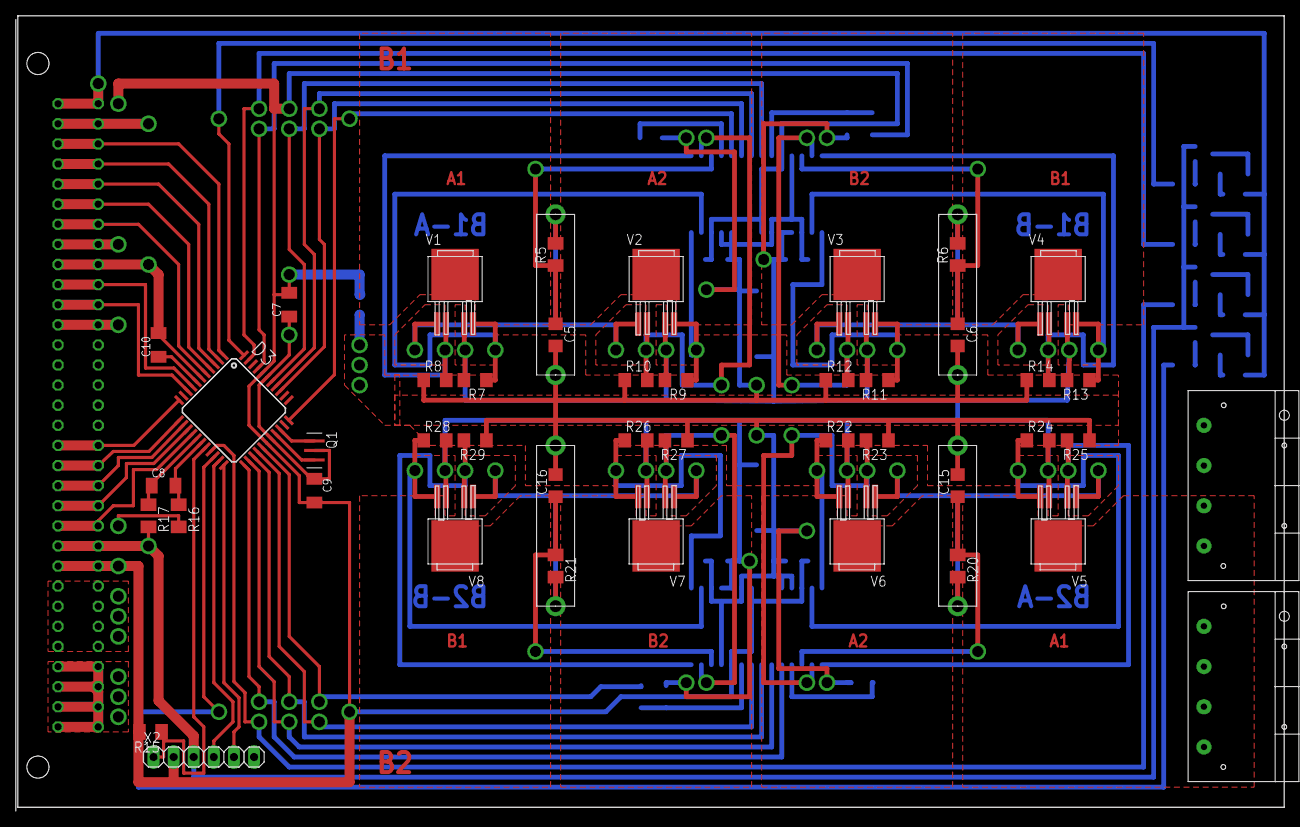
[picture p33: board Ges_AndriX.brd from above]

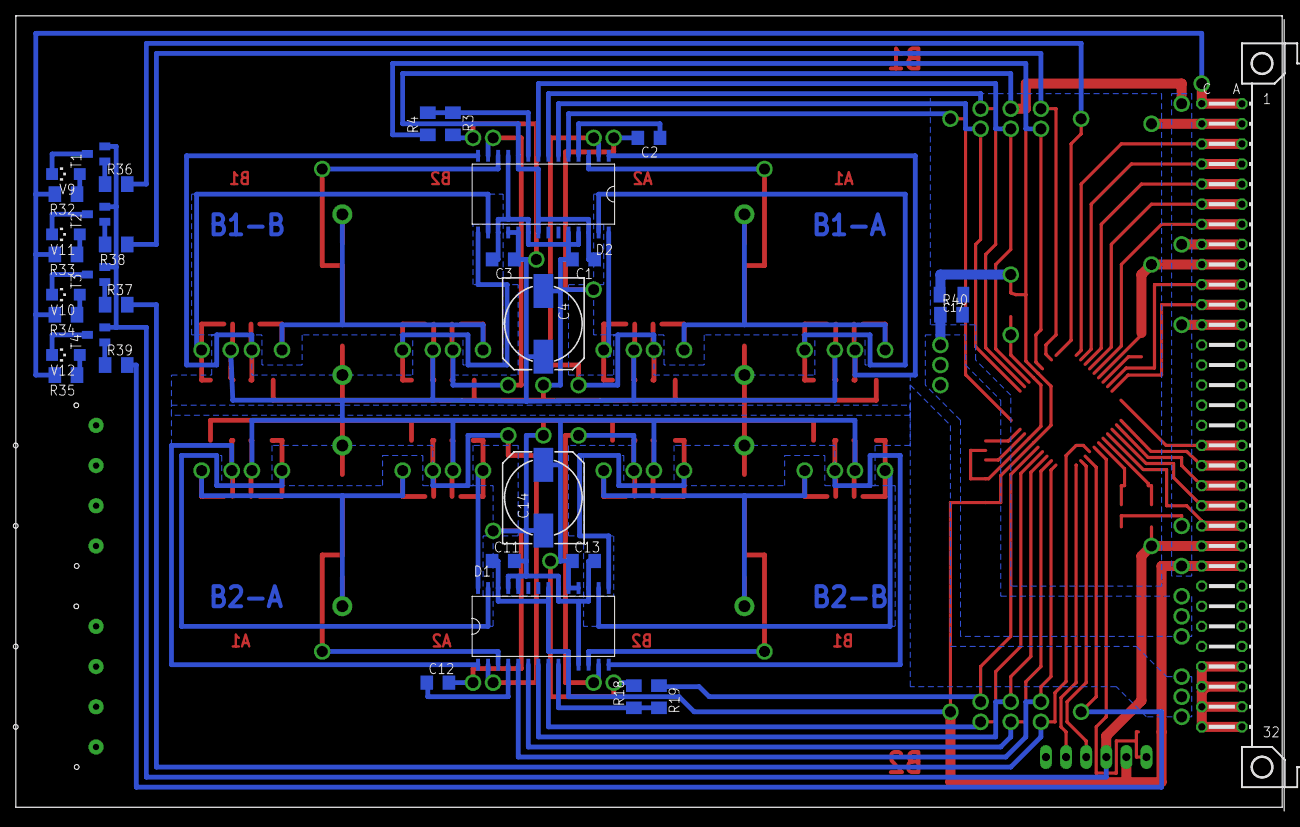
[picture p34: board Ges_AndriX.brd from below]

Board: 2 copper layers, 160.0 x 100.0 mm, 81 parts (33 on the bottom side), 87 nets.

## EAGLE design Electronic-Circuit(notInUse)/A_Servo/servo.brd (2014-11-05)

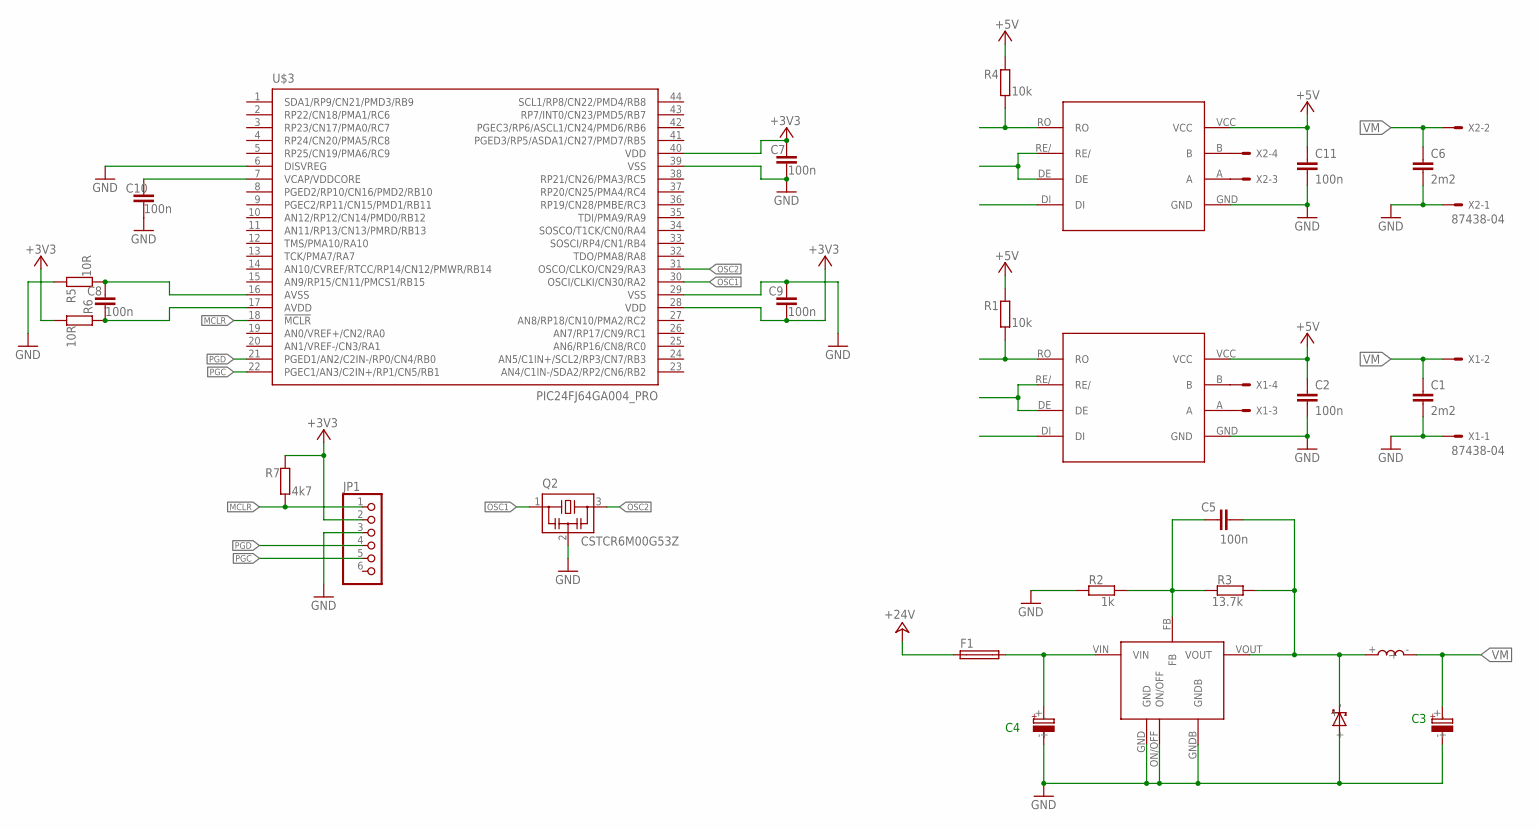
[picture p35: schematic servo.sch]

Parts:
C1, C6: 2m2; C1206
C2, C5, C11: 100n; C1206
C3: 220uF; C220
C4: 680uF; C680
C7, C8, C9, C10: 100n; C1206K
F1: SH22,5
JP1: PINHD-1X6; 1X06
L1: WE-PD
N2, N3: MAX485; SO08
Q2: CSTCR6M00G53Z; CSTER12M
R1, R4: 10k; R1206
R2: 1k; R1206
R3: 13.7k; R1206
R5, R6: 10R; M1206
R7: 4k7; M1206
U$1: LM2596; TO220
U$2: SCHOTTKY
U$3: PIC24FJ64GA004_PRO; TQFP44
X1, X2: 87438-04

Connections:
+3V3: C7.2, C9.2, JP1.2, R6.2, R7.2, U$3.28 (VDD), U$3.40 (VDD)
+5V: C2.1, C11.1, N2.VCC, N3.VCC, R1.2, R4.2
+24V: F1.1
GND: C1.2, C2.2, C3.-, C4.-, C6.2, C7.1, C9.1, C10.2, C11.2, JP1.3, N2.GND, N3.GND, Q2.2, R2.2, R5.2, U$1.GND, U$1.GNDB, U$1.ON/OFF, U$2.-, U$3.6 (DISVREG), U$3.29 (VSS), U$3.39 (VSS), X1.1, X2.1
MCLR: JP1.1, R7.1, U$3.18 (!MCLR)
unnamed: N2.DE, N2.RE/
unnamed: N2.RO, R1.1
unnamed: N2.A, X1.3
unnamed: C8.2, R6.1, U$3.17 (AVDD)
unnamed: N2.B, X1.4
unnamed: C8.1, R5.1, U$3.16 (AVSS)
unnamed: C4.+, F1.2, U$1.VIN
unnamed: C10.1, U$3.7 (VCAP/VDDCORE)
unnamed: C5.1, R2.1, R3.2, U$1.FB
unnamed: C5.2, L1.+, R3.1, U$1.VOUT, U$2.+
unnamed: N3.DE, N3.RE/
unnamed: N3.RO, R4.1
unnamed: N3.B, X2.4
unnamed: N3.A, X2.3
OSC1: Q2.1, U$3.30 (OSCI/CLKI/CN30/RA2)
OSC2: Q2.3, U$3.31 (OSCO/CLKO/CN29/RA3)
PGC: JP1.5, U$3.22 (PGEC1/AN3/C2IN+/RP1/CN5/RB1)
PGD: JP1.4, U$3.21 (PGED1/AN2/C2IN-/RP0/CN4/RB0)
VM: C1.1, C3.+, C6.1, L1.-, X1.2, X2.2

Board: 2 copper layers, 29 parts (0 on the bottom side), 23 nets, no tracks yet.

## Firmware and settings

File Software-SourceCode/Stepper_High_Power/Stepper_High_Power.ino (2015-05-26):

/*
  Name:            Stepper Motor Controller (Serial Communication) - 3.5A low power version
  Autor:           Alexander Wurm, Kevin Pan
  Discribtion:     Stepper Motor Controller (Serial Communication) - 3.5A low power version
  Last Update:     05.2015
  Contact:         kpan@student.tgm.ac.at, awurm@student.tgm.ac.at
*/
#include <LiquidCrystal.h>
//Pin setups:
#define Sensor_Touch_Sensor_Pin 28                              //Touch Sensor(init) pin
#define Motor_Clock_pin	5                               //Clock(Tacks) CLK+ pin
#define Motor_Direction_pin 6                           //Direction CW+ pin
#define Motor_Enable_pin 7
#define Lcd_D7_pin 36
#define Lcd_D6_pin 38
#define Lcd_D5_pin 40
#define Lcd_D4_pin 42
#define Lcd_Enable_pin 11
#define Lcd_RS_pin 12
#define Lcd_Backlight_pin 52

//Static values:
#define Maximum_steps 32250	                        //Maximum steps
#define Axis_length 4950			        //Maximum Length
#define Clock_impuls 100 			        //Microsecond

//Variables:
int Current_position = 0;			        //Milimeter
float Step_resolution = 0.15349;      //Stepmotor step-resolution in mm
String inputString = "";              // a string to hold incoming data
boolean stringComplete = false;       // whether the string is complete
int delayOfMotor = 0 ;
boolean motor_enable;                 // Remembers the status of motor en/disable
LiquidCrystal lcdDisplay(Lcd_RS_pin, Lcd_Enable_pin, Lcd_D4_pin,Lcd_D5_pin,Lcd_D6_pin,Lcd_D7_pin);

void setup() {
  //Lcd Display setup:
  lcdDisplay.begin(16,2);
  pinMode(Lcd_Backlight_pin, OUTPUT);
  lcdBackLightOnOff(true);
  lcdShow("System: Starting","Please Wait...");
  
  //Reserving memory spaces for inputStream:
  Serial.begin(9600);
  inputString.reserve(32);
  
  //Motor pin Setup:
  motor_enable=true;
  pinMode(Motor_Enable_pin,OUTPUT);
  pinMode(Motor_Direction_pin, OUTPUT);
  pinMode(Motor_Clock_pin, OUTPUT);
  pinMode(Sensor_Touch_Sensor_Pin,INPUT);
  digitalWrite(Motor_Enable_pin,LOW);
  digitalWrite(Motor_Direction_pin, LOW);
  digitalWrite(Motor_Clock_pin, LOW);
  delay(2000);

  //
  lcdShow("Reseting  POS.","Please Wait...");
  delay(2000);
  reset();
  
  //Finish Reseting Position:
  lcdShow("Reseting  POS...","Finished...");
  digitalWrite(Motor_Enable_pin,HIGH);
  motor_enable=false;
  delay(1000);
  lcdShow("Waiting Command","_POS");
}

void serialEvent() {
  while (Serial.available()) {
    // get the new byte:
    char inChar = (char)Serial.read();
    // add it to the inputString:
    inputString += inChar;
    // if the incoming character is a newline, set a flag
    // so the main loop can do something about it:
    if (inChar == '@') {
      stringComplete = true;
    }
  }
}

void loop() {
  if (stringComplete) {
    String command=inputString.substring(0,3);
    String showCommand="Command: "+command;
    lcdShow(showCommand,"_POS");
    if(command=="ENA"){
      //Serial.println("motor enabled");
      digitalWrite(Motor_Enable_pin, LOW);
      motor_enable=true;
    }
    else if(command=="DIS"){
      //Serial.println("motor disabled");
      digitalWrite(Motor_Enable_pin,HIGH);
      motor_enable=false;
    }
    else if(command=="RES"){
      //Serial.println("Position resets");
      reset();
    }
    else if(command=="GTP"){
      int pos=inputString.substring(3,inputString.length()).toInt();
      //Serial.print("Going to position: \t");Serial.println(pos);
      goToPosition(pos);
    }
    else if(command=="SST"){
      int del=inputString.substring(3,inputString.length()).toInt();
      //Serial.print("Set delay to: \t");Serial.println(del);
      delayOfMotor=del;
    }
    else if(command=="CTP"){
      String out = String(Current_position) + "@";
      Serial.println(out);
    }
    else if(command=="CTS"){
      if(delayOfMotor==0){
          Serial.println("0@");
        }
      else{
          String out = String(delayOfMotor) + "@";
          Serial.println(out);
        }
    }
    else if(command=="LED"){
      boolean onoff = inputString.substring(3,inputString.length()).toInt();
      lcdBackLightOnOff(onoff);
    }
    else{
      //Serial.println("SYSTEM: Serial input error");
      //Serial.print("Input:\t");
      //Serial.println(inputString);
    }
    
    lcdShow(showCommand,"_POS");
    // clear the string:
    inputString = "";
    stringComplete = false;
  }
}

void reset(){                   //RESET THE POSITION BACK TO 0 USING SENSOR
  if(motor_enable==true){
    digitalWrite(Motor_Direction_pin, HIGH);
    while(!digitalRead(Sensor_Touch_Sensor_Pin)){
      digitalWrite(Motor_Clock_pin, HIGH);
      delayMicroseconds(Clock_impuls);
      digitalWrite(Motor_Clock_pin, LOW);
      delayMicroseconds(Clock_impuls);
      delay(delayOfMotor);
    }
    Current_position = 0;
  }
}

void goToPosition(int x_position){
    if(motor_enable==false){return;}

    //checking if the input value is posible:
    if(x_position<0 || x_position>4950){
      return;
    }

    //calculating the difference:
    int diff = x_position - Current_position;
    if(diff>0){
      digitalWrite(Motor_Direction_pin, LOW);
    }
    else if(diff<0){
      digitalWrite(Motor_Direction_pin, HIGH);
      diff=-diff;
    }
    else {
      return;
    }

    //If the position is going back to zero:(will be repalced with a digital button)
    if(x_position==0){
      int k = (int)(Current_position/Step_resolution);
      for(int i=1;i<=k; i++){
        digitalWrite(Motor_Clock_pin, HIGH);
        delayMicroseconds(Clock_impuls);
        digitalWrite(Motor_Clock_pin, LOW);
        delayMicroseconds(Clock_impuls);
        delay(delayOfMotor);
      }
      Current_position =0;
      return;
    }

    int steps = (int)(diff/Step_resolution);
    for(int i=1;i<=steps; i++){
      digitalWrite(Motor_Clock_pin, HIGH);
      delayMicroseconds(Clock_impuls);
      digitalWrite(Motor_Clock_pin, LOW);
      delayMicroseconds(Clock_impuls);
      delay(delayOfMotor);
    }
    Current_position = x_position;
}

void lcdShow(String outputString1,String outputString2){
  //Cleaning the screen:
  lcdDisplay.clear();
  
  //First row:
  lcdDisplay.setCursor(0, 0);
  lcdDisplay.print(outputString1);
  
  //Second Row:
  lcdDisplay.setCursor(0, 1);
  if(outputString2 == "_POS"){
    String out;
    out = "POS: " + String(Current_position);
    out = out + " mm";
    lcdDisplay.print(out);
  }
  else{
    lcdDisplay.print(outputString2);
  }
}

void lcdBackLightOnOff(boolean a){
  if(a==true){digitalWrite(Lcd_Backlight_pin,HIGH);}
  else if(a==false){digitalWrite(Lcd_Backlight_pin,LOW);}
}

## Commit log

2014-11-05 V1: Everything works with Arduino!!!
    Version 1: Prototype version
    [Ges_AndriX.brd, Ges_AndriX.sch, sensor.sch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]
2015-02-26 Clean up
    [Ges_AndriX.brd, Ges_AndriX.sch, sensor.sch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]
2015-05-26 Finial Cleanup, Officially handed over to PRIA
    [CAD_Assembly.SLDASM, CAD_Assembly.SLDDRW, CKR_110_NN_1_69.SLDASM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]

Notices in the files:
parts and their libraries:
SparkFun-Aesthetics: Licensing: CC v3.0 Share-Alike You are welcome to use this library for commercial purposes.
